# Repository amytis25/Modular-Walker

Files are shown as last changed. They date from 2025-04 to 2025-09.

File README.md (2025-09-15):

ENSC 386 – An Introduction to Mechanical Design and Analysis of Robots

Modular Walker

Due Date: April 27th/ 2025

Amytis Saghafi
asa414@sfu.ca

Simon Schaufele
ses16@sfu.ca

Justin Krohman
jek14@sfu.ca 

Abstract

This project presents the design and analysis of a Modular Walker robot developed to support aging-in-place living. This transformer robot features a modular, self-configurable system that transforms into different modes—walking support, table, and seating—to assist elderly individuals in everyday tasks. Equipped with linear actuators, a call system, and docking capabilities, the design promotes safety, autonomy, and usability. The report outlines the design concept, mechanical analysis, actuation system, and integration within a home environment.
Introduction
The rising elderly population poses challenges for independent living. Robotic systems offer innovative solutions to enhance autonomy and reduce social isolation. This project proposes a transformer robotic system—the Modular Walker—targeted at elderly users who require assistance with mobility, eating, and transitioning between sitting and standing.
Existing Products:
Standard walkers lack dynamic support or smart features.
Sit-to-stand lift chairs offer seating assistance but lack mobility.
Robotic assistants like ElliQ and mobile tables are single-purpose.
Our design combines and extends these functionalities through a reconfigurable robotic system.

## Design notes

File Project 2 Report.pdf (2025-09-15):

ENSC 386 – An Introduction to Mechanical Design and Analysis of Robots

Project 1

# Modular Walker

Due Date: April 27th/ 2025

Contributions

Amytis Saghafi | 301455814 | asa414@sfu.ca | 33%
Simon Schaufele 301454255 | ses16@sfu.ca | 33%
Justin Krohman | 301451597 | jek14@sfu.ca | 33%

## Abstract

This project presents the design and analysis of a Modular Walker robot developed to support aging-in-place living. This transformer robot features a modular, self-configurable system that transforms into different modes—walking support, table, and seating—to assist elderly individuals in everyday tasks. Equipped with linear actuators, a call system, and docking capabilities, the design promotes safety, autonomy, and usability. The report outlines the design concept, mechanical analysis, actuation system, and integration within a home environment.

## Introduction

The rising elderly population poses challenges for independent living. Robotic systems offer innovative solutions to enhance autonomy and reduce social isolation. This project proposes a transformer robotic system—the Modular Walker—targeted at elderly users who require assistance with mobility, eating, and transitioning between sitting and standing.

Existing Products:

- Standard walkers lack dynamic support or smart features.
- Sit-to-stand lift chairs offer seating assistance but lack mobility.
- Robotic assistants like ElliQ and mobile tables are single-purpose.

Our design combines and extends these functionalities through a reconfigurable robotic system.

## Design Problems and Constraints

Design Problem:
To design a multi-purpose robotic walker system that autonomously adapts to support sitting, standing, walking, and meal delivery.

Constraints:

- Must support up to 250 lbs for sitting support.
- Must integrate into typical home layouts.
- Must allow modular reconfiguration and remote control.
- Must use commercially available actuators and parts.

Use Case Layouts & Challenges:

- Bedroom → Living Room
- Supports the user when moving off the bed into a standing position.
- Supports the user when standing as a walker.
- Motorized wheels to alleviate the force required to move the module.
- Supports the user when sitting with back support and a motor lockout to prevent movement.
- Kitchen Docking
- Self-driving to the kitchen station using motors and infrared sensors.
- Automatic alignment with the kitchen module to dock.
- Automatic food delivery onto the walker in table mode.
- Automatic delivery of food to the user using self-driving.
- Challenges
- Navigating cluttered environments with limited sensors.
- Automatic docking and connecting to the bed and kitchen modules.

Design Summary:

- Modular walker with transformable seat/chair
- Bed/chair interface module and kitchen docking.
- Remote summon functionality and self-alignment via sensors.

## Type Synthesis

Considered Concepts:

- Single-purpose walker (too limited)
- Robotic exoskeleton (complex, not modular)
- Multi-purpose transformer walker ✅

After discussing possible ideas for the modular robotic system, it was agreed that the best idea was a multi-purpose walker to support users in a home with the following features:
- Capable of supporting the user as a walker
- Capable of supporting the user as a chair
- Can navigate the living area autonomously
- Walker can switch between walker and chair mode
- Capable of supporting the user in other daily tasks

Walker Module:
- Rigid walker with wheels and sensors to navigate the living area
- Supports the user in navigating the house
- Carrying space to increase the functionality
- Simple design, low functionality, little to no innovation
- Linear actuator walker to switch between a chair & walking mode
- Chair mode allows the user to sit
- Table mode to deliver food
- Moderate complexity, offers innovative support, and is expensive
- Two sets of linear actuators to allow for a floor, chair, & walking
- Chair mode allows the user to sit
- Table mode to deliver food
- More complex design, heavier, & most expensive

Final Concept:
A parallel-bar style modular walker with:
- One set of extendable double-acting cylinders.
- Swappable bed and chair interface modules.
- Docking and delivery module for the kitchen.

## Size Synthesis

### Walker Module

Mode Primary Cylinder Seat/Table Height

Seat | Retracted | 0.58m
Table | Extended | 1m
- Cylinder Stroke: 0.305m
- Total Lift Support: 115kg (safety ratio considered, max support: 185kg)
- Seat Dimensions: 0.4572m x 0.305m
- Dimensions: 0.610m x 0.305m x 0.914m
- Materials: Aluminum frame and supports, canvas seat/table, rubber caster wheels

### Kitchen Module

- Overall Dimensions:
Length: 0.92 m | Width: 0.46 m | Height: 0.20 m
- Base Dimensions:
Length: 0.92 m | Width: 0.43 m | Height: 0.14 m
- Overhang Dimensions:
Length: 0.11 m | Width: 0.46 m | Height: 0.05 m
- Main Belt Length: 1.5641 m
- Secondary Belt Length: 0.2494 m
- Belts Width: 0.32671 m
- Attachment Module: 0.3048 m x 0.2032 m
- Module Mass: 17.5 kg
- Weight Allowance: 7 kg rated, 25 kg max
- Materials: ⅓ infill PC-ABS ( blend of Polycarbonate (PC) and Acrylonitrile Butadiene Styrene (ABS)) Frame, ¼ infill Aluminum Alloy rollers and motor enclosure, rubber belts

### Bed Module

- Contracted Position Dimensions
Length: 0.13m | Width: 0.38 m | Height: 0.44m
- Extended Position Dimensions
Length: 0.13m | Width: 0.38 m | Height: 0.59m
- Bed Frame Hanger: 0.381 m x 0.127 m x 0.0508 m
- Electrical Actuators: 0.279 m x 0.432 m x 0.0381 m
- Wheel Bed: 0.114 m x 0.0381 m x 0.029 m
- Module Mass: 4.83 kg
- Actuator Stroke Length: 0. 152 m
- Materials: Aluminum frame supports supports Aluminum Actuators and Polyethylene Wheelbed

## Detailed Component Design

### Modules & Features:

- Main Frame: Parallel bar design with height-changing table.
- Cylinders:
- Primary: 102 lbs force @ 100 psi
- Support Beam: Reinforced crossbeam at the top and bottom of the cylinders.
- Piston Mounts: Mounts directly to the base and crossbeams
- Remote & Sensor Unit: Bluetooth or Wi-Fi controlled; IR or ultrasonic for alignment.

### Module 1 - Walker Module

Configurations:
- Walker mode - Seat at 0.585m, Wheels moving
- Chair mode - Seat at 0.585m, Wheels locked out
- Table mode - Seat at 1m, Wheels moving, Locked out wheels at Kitchen and Bed module

Size:

Length: 0.56 m | Width: 0.33 m | Height: 1.02 m

Materials:

- Aluminium components

Movement:

The module moves using two motors for the front two wheels. The wheels rotate as the walker is pushed in walker mode. Infrared sensors guide the module to the required location, allowing it to move autonomously. The module can self-drive between the kitchen, bed, and the user. The user can control the module with a remote, which can change the configuration or send it to a location.

### Module 2 - Kitchen Module

Configuration:

- The base portion of the module lies on top of the kitchen counter with the overhang portion resting against the side of the counter.
- The overhang portion includes a proximity sensor and electromagnets. The proximity sensor activates the electromagnets to hold the walker in place as the module moves an object (e.g., a plate of food) onto the walker.

Size:

- Overall:
Length (x): 0.92 m | Width (y): 0.46 m | Height (z): 0.20 m
- Base:
Length (x): 0.92 m | Width (y): 0.43 m | Height (z): 0.14 m
- Overhang:
Length (x): 0.11 m | Width (y): 0.46 m | Height (z): 0.05 m
Materials:
- PC-ABS ( blend of Polycarbonate (PC) and Acrylonitrile Butadiene Styrene (ABS))
- Aluminium Alloy
- Rubber

Movement:

This module uses a compact DC motor to rotate the first set of rollers attached to the motor using bevel gears. The main belt of this module rotates around the rollers, carrying an object (a plate filled with food) to the next belt, which will move with the force of the object's already existing acceleration as well as the force of gravity, as the secondary belt has approximately a 20-degree decline. Following the second belt, the object will be smoothly pushed onto the “table” portion of the walker.

Attachment:

Attaches to the kitchen module using electromagnets, and a sensor detects the walker's presence.

### Module 3 - Bed Module

Configuration:
- Compacted: The actuators are retracted to reduce the footprint of the module
- Extended: The IR Sensors have detected that the module has been deployed and signal the Arduino to self configure
Size
Length: 0.13m | Width: 0.38 m | Height: 0.59m

Materials: Aluminum alloy and Polyethylene
Movement: Two Electrical actuators receive a signal from IR sensors in the modules hanging attachment. This signals them that the module has been deployed. The actuators then lengthen to fit the size of the bed frame that the module is attached to.
Attachment: The Walker Attaches to the bed module using electromagnets and a sensor to detect the walkers presence

## Specifications

Actuators:
Walker Module
- McMaster Impact-Resistant Round Body Air Cylinders (https://www.mcmaster.com/6471K334/)
- Air-driven, 102 lbs @ 100 psi each
- Mounted with guiding rails and locking mechanisms
- Air compressor (https://www.amazon.ca/HOTTQUE-Multifunctional-Inflator-Compressor-Motorcycle/dp/B0DFM3JPHX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)
- Motors (https://ca.robotshop.com/products/e-s-motor-12v-16rpm-high-torque-dual-shaft-31d-motor-w-worm-gear-reduction-with-customized-connector-terminations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)
- Front Wheels, (https://ca.robotshop.com/products/sparkfun-wheel-65mm-rubber-tire-pair?qd=a9e12b3ea89f7583d59347062a0848af) Back (https://www.rona.ca/en/product/madico-general-duty-rubber-plate-caster-brake-44-lbs-1-1-2-f22904-01015307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) Wheels
Kitchen Module
- Compact Round-Face DC Motor (https://www.mcmaster.com/6331K65/)
- Motor Speed: 4535 rpm @ 0.0812 N-m
- Starting Torque: 0.5437 N-m
- Required torque: 4.14 N-m
■ τ
required = F
friction
| × radius = 9. 81M
Max
| | × µ = 108. 69 × 0. 5 = 4. 14
■ Note: This calculation is for an unlubricated system; a lubricated system would need significantly less torque.
- Roller Gear to Motor Gear ratio: 8:1
- 5V Electromagnet (https://www.digikey.ca/en/products/detail/adafruit-industries-llc/3874/9603613)

Bed Module

- McMaster Electric Actuator (https://www.mcmaster.com/6509K56/)
- 11.3kg Dynamic load capacity
- 136kg static load capacity
- Maximum speed 76.2mm/s
- 5V Electromagnet
Motion Transmission:
- Linear lifting via cylinder extension (Walker Module)
- Load transfer through piston brackets and reinforced beams (Walker Module)
- Rotational motion transmission via bevel gears (Kitchen Module)

Control Source:
- IR Sensors (https://www.amazon.ca/C-J-Infrared-Obstacle-Avoidance-Arduino/dp/B00XAGSWR4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)
- Arduino Uno (https://www.amazon.ca/Elegoo-Board-ATmega328P-ATMEGA16U2-Arduino/dp/B01EWOE0UU?hvadid=208414040833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)
- ROS-based command structure

## Case Study Static Analysis

### Walker Module

Payload:
- Max load: 250 lbs = 1113 N
- Cylinder support force: 400 lbs = 1780 N
- Safety ratio: 1.6
Weight:
- Walker module total mass: 21kg = 206.01 N
- Seat mass: 2kg = 19.62 N
- Cylinder mass: 1.5kg = 14.715 N (each)
- Base mass: 7.5kg = 73.575 N
- Supports mass: 6kg = 58.86 N
Tipping Analysis:
- Consider CoG shift during transformation
- Counterbalanced base and locking wheels prevent forward tipping
- Simulation to confirm balance under 40” extended table height with load

Static stability analysis:
Centre of mass location: X - .200m Y - .380m Z - .125m (related to the bottom wheel)
Angle of tipping: Θ = arctan( | (tipping can only occur around the z-axis as the .200
.380

) = 27. 76°
module would roll in any other direction)
Max Horizontal Force: Θ＜arctan(

Max Force
Total Mass

)
Max Force = 206 tan(27. 76°) = 108. 5N

### Kitchen Module

Payload:
- Max load: 25 kg
Weight:
- Kitchen module total mass: 17.5 kg = 171.675 N
- Frame mass: 6.23 kg = 61.1163 N
- Rollers mass: 9.56 kg = 93.7836 N
- Main belt mass: 1.08 kg = 10.5948 N
- Secondary belt mass: 0.09 kg = 0.8829 N
- Motor and enclosure mass: 0.27 kg = 2.6487 N Attached Actuators:
- 2x electromagnets

Static Stability Analysis:
Center of mass relative to the back bottom corner of the base: X = 0.47 m, Y = 0.2 m, Z = 0.06 m For the structure to tip over, the center of gravity's X component must be located past 0.75 m. To see how much weight would shift the center of gravity past the tipping point, the following calculations were done:

X

tip =

mstructure

x

structure +mobjectx
object
mstructure+mobject

→ 0. 75 =

(17.5)(0.47)+(0.92)mobject

17.5+mobject

Solving for mobject

, it is determined that the object must weigh 28.8 kg or more to cause the module to tip over and fall off the counter when the object reaches the end of the belt. Since the module has a maximum load capacity of 10 kg, tipping over is not a concern.

To make sure the object won’t slip off the secondary belt, the maximum acceleration of the object can be calculated as shown below (note: the coefficient of static friction between dry glass and rubber was used):

ΣF = ma → F

friction = ma → 9. 81sin(20)m = ma → a = 0. 73 m/s

2

As shown above, the maximum acceleration allowed is 0.73 m/s² to prevent the object from slipping on the belt's surface.

### Bed Module

Payload:
- Max Load: 300 lbs = 1335 N Weight:
- Arduino uno: 11.83 g = 0.1160523 N
- Hanging frame: 2.98 kg = 29.2338 N
- Electromagnets: 22.2 g = 0.217782 N
- Electric actuators: 1.72 kg = 16.8732 N
- Wheelbeds = 94.5 g = 0.927045 N Attached Actuators:
- 2x electromagnets
- 2x Linear Actuators

Static Stability Analysis:
The center of mass relative to the back corner of the left wheel bed:
X = 18.67cm, Y = 42.79cm, Z = 0.88cm
The bed module is suspended from the bed frame, and the wheel beds rest on the ground. This means that, to tip the bed module, it would either need to be disconnected from the bed frame or the bed frame itself would have to tip over. Therefore, the tipping point is determined by the stability of the bed frame. The module itself is not designed to support any weight other than the walker wheels in the wheel beds, which are in contact with the ground. Since this weight is also supported by the ground, the maximum load on the module would be the combined weight of the walker module and the person.
The pressure exerted by one of the wheels when the person leans on it is approximately one quarter of the combined weight of the person and the walker (75lb). Given that the compressive strength of polyethylene is about 3000 psi (20.7MPa), the wheel beds can support the maximum payload without any deformation. This is shown below (note: wheel bed area = 1.69 in²
):
σ =

F
A

→ σ =

2413
1.69 = 1427 psi
This is much less than the allowable compression strength of the wheel bed.

## Image and Animated Videos

Note: Videos of the modules can be viewed in the project folder under images directory/ animation, as they cannot be added to this document.

### Walker Design

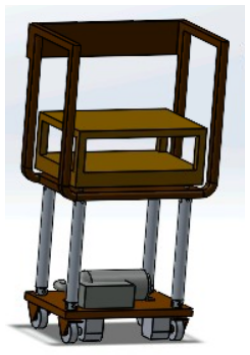
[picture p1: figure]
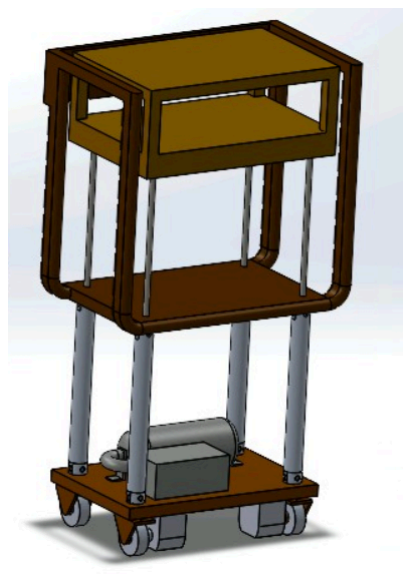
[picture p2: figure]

Chair & Walker Configuration | Table Configuration

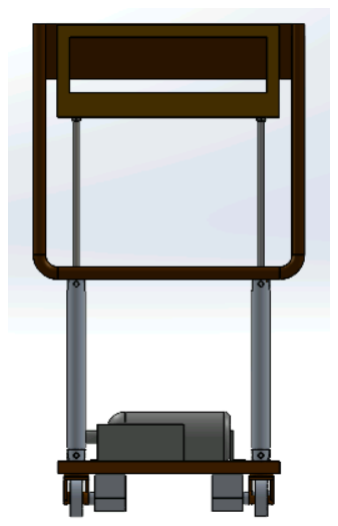
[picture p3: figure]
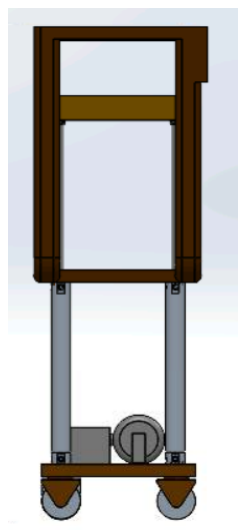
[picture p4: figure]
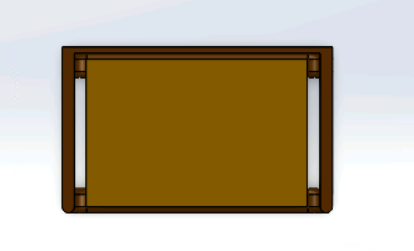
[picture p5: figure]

Front View | Side View | Top View

### Kitchen Module

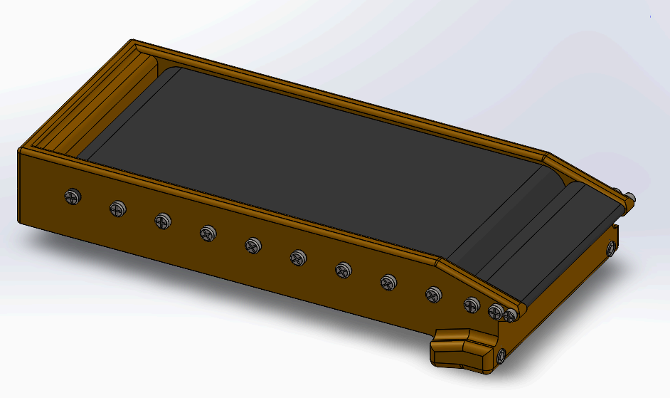
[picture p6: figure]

Kitchen Module Simulation

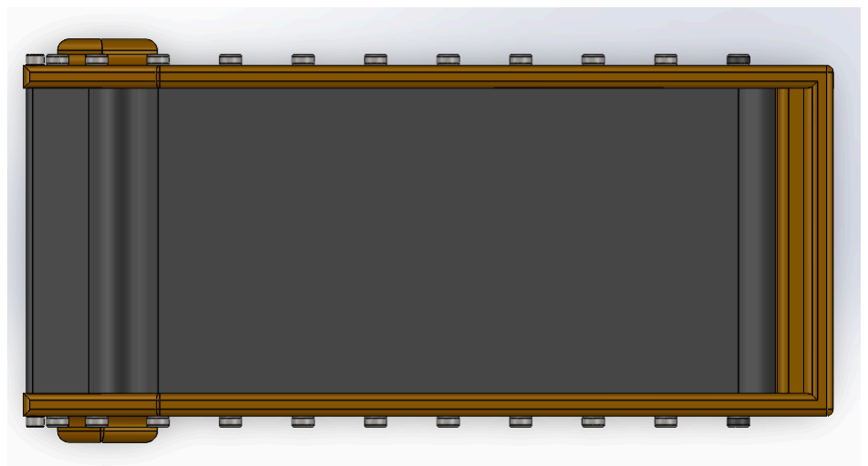
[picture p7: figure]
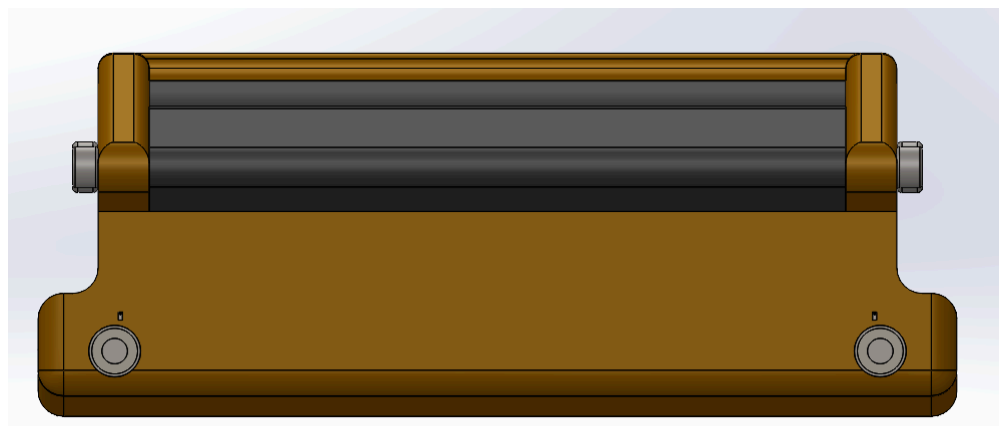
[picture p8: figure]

Top View of the Kitchen Module | Front View of the Kitchen Module

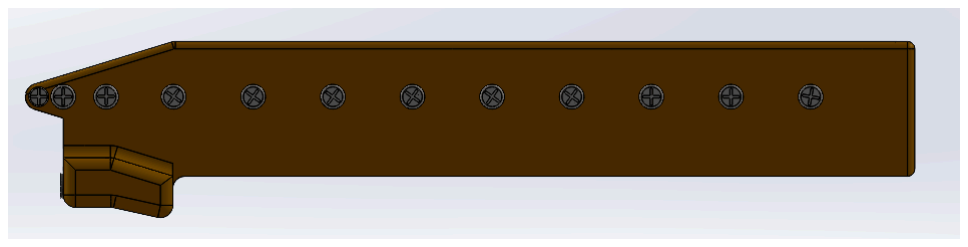
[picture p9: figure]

Side View of the Kitchen Module

The hidden lines visible model shown below shows More Detail, including pathways for wiring and cavities for circuitry, batteries, fans, etc.

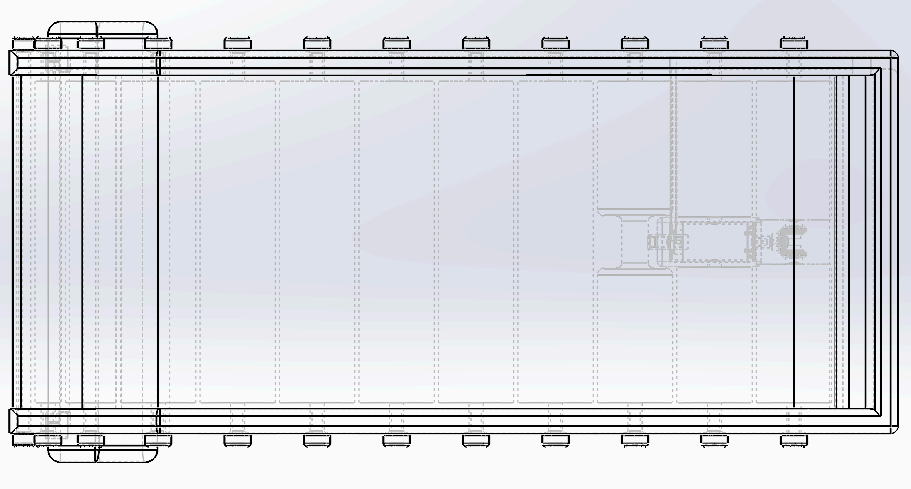
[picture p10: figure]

Top View of the Kitchen
Module

Side View of the Kitchen
Module

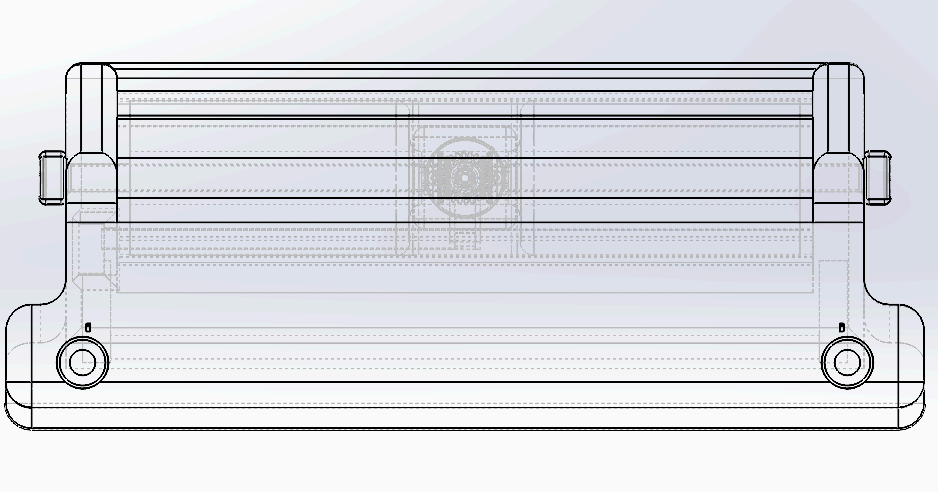
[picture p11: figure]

Front View of the Kitchen
Module

### Bed Module

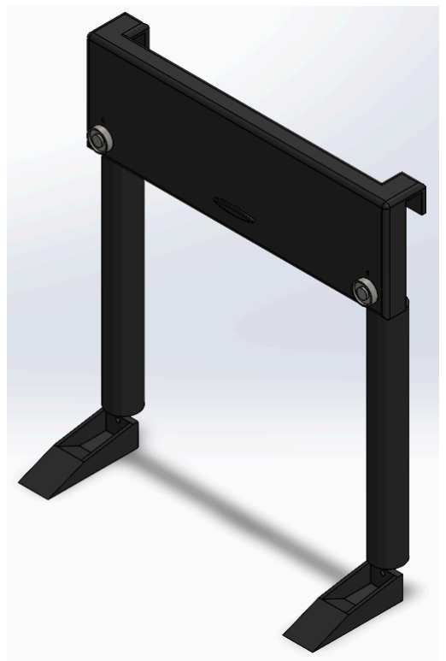
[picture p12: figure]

Bed Module Simulation

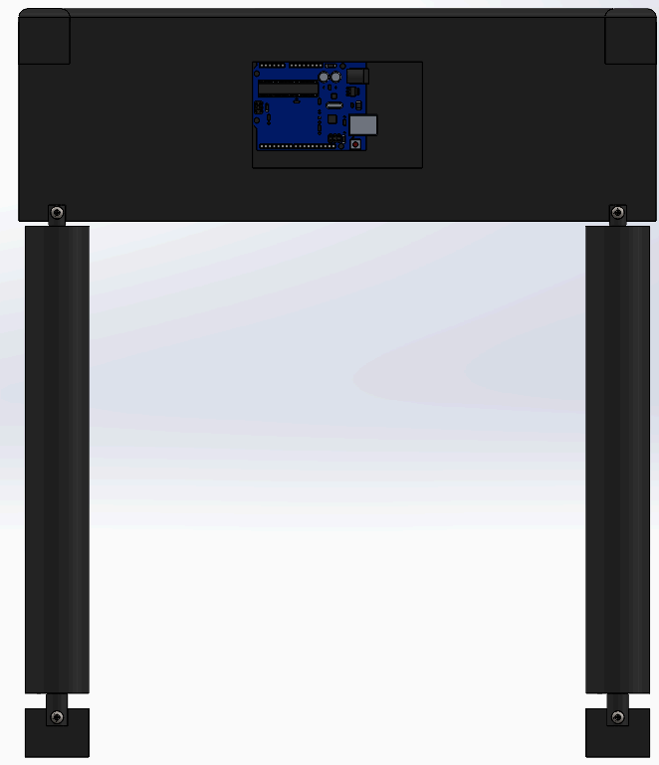
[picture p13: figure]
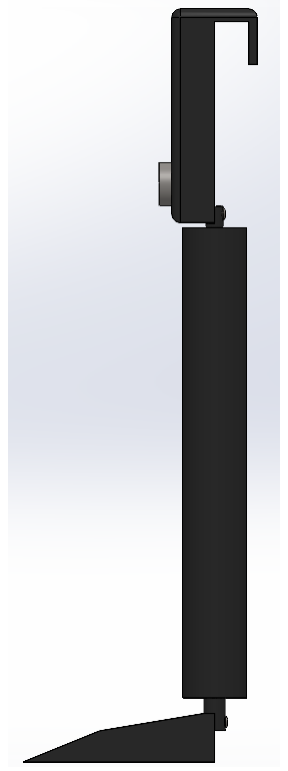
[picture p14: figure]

Side View of the Bed Module | Front View of the Bed Module

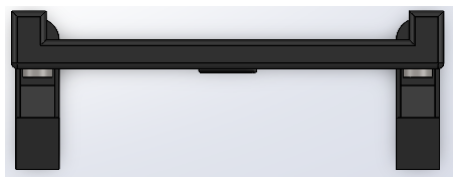
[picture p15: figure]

Top View of the Bed Module

## Discussion and Future Work

The Modular Walker fulfills key functions for elderly care in a modular form. The design fulfills all the functionalities specified in the synthesis design, which supports the user moving around their home and performing daily tasks like food delivery. These functions are fulfilled using three modules: the walker module, the bed module, and the kitchen module.

The walker module is the primary component that the user interacts with. This module supports the user when moving around their home and provides a place to sit anywhere. The walker can be summoned or its configuration changed using a Wi-Fi button remote.

The bed module connects to the walker and provides a place for the walker to be stored and charged when not in use. It can also help the user get out of bed and into a standing or seated position on the walker.

The kitchen module connects to the walker through electromagnets. This connection ensures the walker's position is accurate and provides a direct connection to ensure the walker is in the correct configuration. This module delivers food onto the walker, placing a plate onto the walker in table mode. The walker then disconnects from the kitchen module and autonomously delivers the food to the user.

Future improvements include:

- A more stable design which is not prone to tipping
- Battery-powered air compressor for cylinder actuation
- Enhanced sensor fusion for better alignment
- Voice control or integration with smart home systems
- Enhanced wheel design to navigate around tight spaces and corners
- An adjustable seat height to maximize the comfort of the user
- More sensors, such as load cells, to allow more accuracy while completing tasks
- i.e. load cell kitchen module to ensure full transfer of object.

## References

[1]
“12V 16rpm High Torque Dual Shaft 31D Motor w/ Worm Gear Reduction, with customized connector terminations,” RobotShop Canada. Accessed: Apr. 26, 2025.
[Online]. | | Available:
https://ca.robotshop.com/products/e-s-motor-12v-16rpm-high-torque-dual-shaft-31d-moto r-w-worm-gear-reduction-with-customized-connector-terminations (https://ca.robotshop.com/products/e-s-motor-12v-16rpm-high-torque-dual-shaft-31d-motor-w-worm-gear-reduction-with-customized-connector-terminations)
| | [2]
“3874 Adafruit Industries LLC | Maker/DIY, Educational | DigiKey.” Accessed: Apr. 26,
2025. | [Online]. | Available:
https://www.digikey.ca/en/products/detail/adafruit-industries-llc/3874/9603613
| | [3]
“DAOKI 5-Pack IR Infrared Obstacle Avoidance Sensor Module for Arduino Smart Car Robot 3 Wire : Amazon.ca: Tools & Home Improvement.” Accessed: Apr. 26, 2025.
[Online]. | | Available:
https://www.amazon.ca/C-J-Infrared-Obstacle-Avoidance-Arduino/dp/B00XAGSWR4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 (https://www.amazon.ca/C-J-Infrared-Obstacle-Avoidance-Arduino/dp/B00XAGSWR4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)
| | [4]
“ELEGOO UNO R3 Board ATmega328P with USB Cable(Arduino-Compatible) for Arduino : Amazon.ca: Electronics.” Accessed: Apr. 26, 2025. [Online]. Available: https://www.amazon.ca/Elegoo-Board-ATmega328P-ATMEGA16U2-Arduino/dp/B01EWOE0UU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 wFPTQYc-R2bbAitwRYlXgVksVoz7wd1v5umHaJ4wKbGjXJ9GZJfEifSVXSnIDzPoZx FHzU.V25m7TA22pPwS6tTp7w2oaZO8PYytDoRU5MG3Xz9_y8&dib_tag=se&hvadid= 208414040833&hvdev=c&hvlocphy=9001527&hvnetw=g&hvqmt=e&hvrand=24032207 0627911368&hvtargid=kwd-295449705573&hydadcr=20846_9881421&keywords=ardui no&mcid=f5570030f4b73130814adeb55dc1fd80&qid=1744753651&sr=8-2-spons&sp_cs d=d2lkZ2V0TmFtZT1zcF9hdGY&psc=1 (https://www.amazon.ca/Elegoo-Board-ATmega328P-ATMEGA16U2-Arduino/dp/B01EWOE0UU?hvadid=208414040833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)

[5]
“HOTTQUE Multifunctional Tire Inflator Portable Air Compressor Cordless Tire Inflato 150 PSI with Digital Pressure Gauge 12V Smart Air Pump for Car Tires, Motorcycle, SUV, Bicycle, Sports Balls…, Air Compressors - Amazon Canada.” Accessed: Apr. 26,
2025. | | [Online]. | | | | Available:
https://www.amazon.ca/HOTTQUE-Multifunctional-Inflator-Compressor-Motorcycle/dp/B0DFM3JPHX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 (https://www.amazon.ca/HOTTQUE-Multifunctional-Inflator-Compressor-Motorcycle/dp/B0DFM3JPHX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)
| | | | | | [6]
“MADICO General-Duty Rubber Plate Caster - Brake - 44 lbs - 1 1/2" F22904 | RONA.”
Accessed: | Apr. | 26, | 2025. | [Online]. | Available:
https://www.rona.ca/en/product/madico-general-duty-rubber-plate-caster-brake-44-lbs-1-1-2-f22904-01015307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 QjwiLLABhCEARIsAJYS6ukSUs28AxclCiFWawiKpM8Q-xoJayHchAjmwjO3-tk8eWZ v9tO-bqYaAgNpEALw_wcB&gclsrc=aw.ds (https://www.rona.ca/en/product/madico-general-duty-rubber-plate-caster-brake-44-lbs-1-1-2-f22904-01015307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)
| | | | | | [7]
“McMaster-Carr.” | Accessed: | Apr. | 26, | 2025. | [Online]. | Available:
https://www.mcmaster.com/6509K56/
| | | | | | [8]
“McMaster-Carr.” | Accessed: | Apr. | 26, | 2025. | [Online]. | Available:
https://www.mcmaster.com/6331K65/
| | | | | | [9]
“McMaster-Carr.” | Accessed: | Apr. | 26, | 2025. | [Online]. | Available:
https://www.mcmaster.com/6471K334/
| | | | | | [10]
“Sparkfun Wheel - 65Mm (Rubber Tire, Pair),” RobotShop Canada. Accessed: Apr. 26,
2025. | | [Online]. | | | | Available:
https://ca.robotshop.com/products/sparkfun-wheel-65mm-rubber-tire-pair

## Appendices

### Appendix A - SolidWorks Files

A.1 Walker Module

Air_Compressor.SLDPRT - Air compressor to refill the air storage Air_Storage.SLDPRT - Air storage compartment Base_6471k334_Impact-Resistant Round Body Air Cylinder.SLDPRT - Base of the cylinders
Rod_Cylinder.SLDPRT - The extending cylinder rod
Cylinder_Top_Plate.SLDPRT - The top plate and arm supports
Motor.SLDPRT - Motors for the front wheels Seat_Table2.SLDPRT - The Seat and Table the changes height Wheel.SLDPRT - Wheels for the base
Assem2.SLDASM - Fully Assembled design of the walker

A.2 Kitchen Module
0.5in-roller.SLDPRT - 0.5 inch roller 1in-roller.SLDPRT - 1 inch roller
2in-roller.SLDPRT - 2 inch roller
3in-roller.SLDPRT - 3 inch roller
3in-roller-gear-attachment.SLDPRT - 3 inch roller which attaches to a Metal bevel Gear
3in-roller-motor-attachment.SLDPRT - 3 inch roller which attaches to a the side of the motor enclosure
3in-roller-motor-cutout.SLDPRT - 3 inch roller with the middle thinned out to allow for the motor enclosure
6331K65_Compact Round-Face DC Motor.SLDPRT - Model of the DC motor (from Manufacturer)
6529K53_Metal Miter Gear.SLDPRT - Model of a bevel gear motorbox.SLDPRT - Enclosure for the motor housing.SLDPRT - Frame and base for the entire module motor-gear-connector.SLDPRT - A piece for motor and bevel gear connection electromagnet.SLDPRT - Rough model of the 5V Electromagnet sensor.SLDPRT - Rough model of the proximity sensor
plate.SLDPRT - Rough model of a plate for simulation purposes boxed-motor.SLDASM - Assembly of the enclosed motor final-assembly.SLDASM - Complete assembly of the kitchen module

A.3 Bed module

hanger.SLDPRT - Hangs the module to the frame of the user’s bed Arduino_Uno.STEP - Model of Arduino Uno (from Manufacturer)
screw.SLDPRT - Screw used for assembling the module
piston rod.SLDPRT - Extending rod of the electric actuator
wheelbed.SLDPRT - Holds the wheels of the walker stable when it is docked at the bed module
piston body.SLDPRT - Aluminum body of the electric actuator
electromagent.SLDPRT - Rough model of the 5V Electromagnet Arduino_Uno.SLDPRT - Model of Arduino Uno (from Manufacturer) Assem1.SLDASM - Final Assembly of the bed module

### Appendix B – Technical specification of the selected actuators and sensors

B.1 Actuators

B.1.1 Walker Module
Actuator 1: McMaster Impact-Resistant Round Body Air Cylinders
- Part Number: 6471K334
- Type: Double-acting pneumatic cylinder
- Force: 102 lbs (454 N) @ 100 psi
- Stroke: 0.305 m (12 inches)
- Mounting: Guided rails with locking mechanism
- Safety Ratio: 1.6 (max support: 185 kg / 408 lbs)
- Application: Seat/table height adjustment (0.58m retracted → 1m extended).
- Vendor: McMaster-Carr
Actuator 2: Air Compressor
- Type: Portable electric air compressor (to power cylinders)
- Pressure: 100 psi minimum
- Duty Cycle: Continuous (for repeated actuation)
- Future Upgrade: Battery-powered compressor (e.g., VIAIR 90P).

B.1.2 Kitchen Module
Actuator 1: Compact Round-Face DC Motor
- Part Number: 6331K65
- Speed: 4535 RPM @ 0.0812 N-m
- Starting Torque: 0.5437 N-m
- Gear Ratio: 8:1 (motor-to-roller)
- Output Torque: 4.14 N-m (after gearing)
- Application: Drives kitchen module’s main belt for food transfer.
- Vendor: McMaster-Carr
Actuator 2: 5V Electromagnets
- Holding Force: 10 kg (per magnet)
- Voltage: 5V DC
- Quantity: 2 (for docking alignment)
- Application: Secures walker module to kitchen station during food transfer.
- Vendor: Digikey

B.1.3 Bed Module
Actuator 1: Electric Linear Actuator
- Type: Battery-powered linear actuator (to replace pneumatic cylinders)
- Stroke: 0.152 m
- Load Capacity: 300 lbs (136 kg)
- Speed: 76 mm/s (adjustable)
- Application: Delopy the wheel beds

Actuator 2: 5V Electromagnets
- Holding Force: 10 kg (per magnet)
- Voltage: 5V DC
- Quantity: 2 (for docking alignment)
- Application: Secures walker module to kitchen station during food transfer.
- Vendor: Digikey
B.2 Sensors

B.2.1 Walker Module
Sensor 1: Infrared (IR) Proximity Sensors
- Type: IR reflectance sensor
- Detection Range: 0.1–0.8 m
- Interface: Digital I/O
- Application: Autonomous navigation and alignment with bed/kitchen modules. Sensor 2: Wheel Encoders
- Type: Optical rotary encoder (integrated with motors)
- Resolution: 12 pulses per revolution (PPR)
- Application: Speed/distance tracking for motorized wheels.

B.2.2 Kitchen Module
Sensor 1: Proximity Sensor With Interrupt, IRED, and I2C Interface
- Part Number: 751-VCNL3040TR-ND - Tape & Reel (TR)
- Detection Range: 0–300 mm
- Interface: I2C
- Application: Detects walker module for docking alignment.
- Vendor: DigiKey/RobotShop

B.2.3 Bed Module
Sensor 1: Proximity Sensor With Interrupt, IRED, and I2C Interface
- Part Number: 751-VCNL3040TR-ND - Tape & Reel (TR)
- Detection Range: 0–300 mm
- Interface: I2C
- Application: Detects walker module for docking alignment.
- Vendor: DigiKey/RobotShop
B.3 Controllers

Controller 1: Raspberry Pi 4
- Processor: Broadcom BCM2711 (Quad-core Cortex-A72)
- RAM: 4GB
- Connectivity: WiFi/Bluetooth
- Role: ROS-based navigation, sensor fusion, and user command processing.

Controller 2: Arduino Uno
- Microcontroller: ATmega328P
- Clock Speed: 16 MHz
- Analog Inputs: 6
- Role: Real-time motor control, sensor polling, and electromagnet activation.

### Appendix C - Suggestions for supporting hardware and electronics

C.1 Controllers

1. Raspberry Pi 4
- Part Number: N/A (Standard model)
- Description: Quad-core Cortex-A72 processor, 4GB RAM, Wi-Fi/Bluetooth.
- Purpose: ROS-based navigation, sensor fusion, and user command processing.
- Supplier: Electronics retailers (e.g., Amazon, Adafruit).
2. Arduino Uno
- Part Number: ELEGOO UNO R3 [4]
- Description: ATmega328P microcontroller, 16 MHz clock speed.
- Purpose: Real-time motor control, sensor polling, and electromagnet activation.
- Supplier: Amazon.
C.2 Sensors
1. Infrared (IR) Proximity Sensors
- Part Number: DAOKI 5-Pack IR Sensor [3]
- Description: 3-wire IR reflectance sensor, 0.1–0.8 m range.
- Purpose: Autonomous navigation and docking alignment.
- Supplier: Amazon.
2. Proximity Sensor (I2C Interface)
- Part Number: 751-VCNL3040TR-ND [2]
- Description: IRED sensor with 0–300 mm detection range.
- Purpose: Precise alignment for kitchen and bed module docking.
- Supplier: DigiKey.
3. Wheel Encoders
- Part Number: Integrated with motors (e.g., Sparkfun wheels [10]).
- Description: Optical rotary encoder, 12 PPR resolution.
- Purpose: Speed/distance tracking for motorized wheels.

C.3 Actuators
1. Double-Acting Pneumatic Cylinders
- Part Number: McMaster 6471K334 [7]
- Description: 102 lbs force @ 100 psi, 0.305 m stroke.
- Purpose: Walker seat/table height adjustment.
- Supplier: McMaster-Carr.
2. Electric Linear Actuators
- Part Number: McMaster 6509K56 [8]
- Description: 136 kg static load capacity, 76.2 mm/s speed.
- Purpose: Bed module deployment.
- Supplier: McMaster-Carr.
C.4 Motors
1. Compact DC Motor (Kitchen Module)
- Part Number: McMaster 6331K65 [8]
- Description: 4535 RPM, 0.5437 N-m starting torque.
- Purpose: Drives kitchen conveyor belt via 8:1 gear ratio.
- Supplier: McMaster-Carr.
2. Wheel Motors
- Part Number: 12V 16RPM High Torque Motor [1]
- Description: Worm gear reduction, dual shaft.
- Purpose: Front-wheel drive for walker module.
- Supplier: RobotShop.
C.5 Power and Communication
1. Portable Air Compressor
- Part Number: HOTTQUE Cordless Inflator [5]
- Description: 100 PSI, battery-powered.
- Purpose: Pneumatic cylinder actuation.
- Supplier: Amazon.
2. 5V Electromagnets
- Part Number: Adafruit 3874 [2]
- Description: 10 kg holding force.
- Purpose: Secures walker during docking.
- Supplier: DigiKey.
3. Wi-Fi/Bluetooth Module
- Description: ESP32 or similar.
- Purpose: Remote control and ROS integration.

C.6 Safety and Miscellaneous
1. Emergency Stop Button
- Description: Physical kill switch for immediate shutdown.
2. Load Cells
- Purpose: Future upgrade for weight detection (e.g., kitchen module).
3. Rubber Belts and Rollers
- Part Number: Custom (see Appendix A.2).
- Supplier: McMaster-Carr/3D-printed.

### Appendix D - Bill of Materials

D.1 Walker Module

Component | Qty | Part Number | Description | Supplier
Linear Actuators | 2 | 6471K334 [7] | Double-acting pneumatic cylinders | McMaster-Carr
Rubber Caster Wheels | 4 | MADICO F22904 [6] | 1.5" brake wheels, 44 lbs capacity | RONA
IR Proximity Sensors | 4 | DAOKI 5-Pack [3] | Obstacle avoidance | Amazon
Arduino Uno | 1 | ELEGOO UNO R3 [4] | Microcontroller | Amazon
Air Compressor | 1 | HOTTQUE [5] | 100 PSI portable compressor | Amazon
Aluminum Frame | 1 | Custom | 6061-T6 aluminum bars | Local supplier
Canvas Seat | 1 | Custom | 0.4572m x 0.305m seat | Fabric supplier

D.2 Kitchen Module

Component | Qty | Part Number | Description | Supplier
DC Motor | 1 | 6331K65 [8] | Compact round-face motor | McMaster-Carr
Bevel Gears | 3 | 6529K53 [A.2] | Metal miter gears for 8:1 ratio | McMaster-Carr
Proximity Sensor | 2 | 751-VCNL3040T R-ND [2] | I2C IR sensor for docking | DigiKey
Electromagnets | 2 | Adafruit 3874 [2] | 5V holding magnets | DigiKey
PC-ABS Frame | 1 | Custom | 3D-printed frame (⅓ infill) | Local printer
Rubber Belts | 2 | Custom | 0.32671m width | McMaster-Carr

D.3 Bed Module

Component | Qty | Part Number | Description | Supplier
Electric Linear Actuators | 2 | 6509K56 [8] | 136 kg static load capacity | McMaster-Carr
Polyethylene Wheelbeds | 2 | Custom | 3D-printed supports | Local printer
Electromagnets | 2 | Adafruit 3874 [2] | 5V holding magnets | DigiKey
Arduino Uno | 1 | ELEGOO UNO R3 [4] | Microcontroller | Amazon
Aluminum Hangers | 1 | Custom | 0.381m x 0.127m frame | Local supplier
Proximity Sensor | 4 | 751-VCNL3040T R-ND [2] | I2C IR sensor for docking | DigiKey

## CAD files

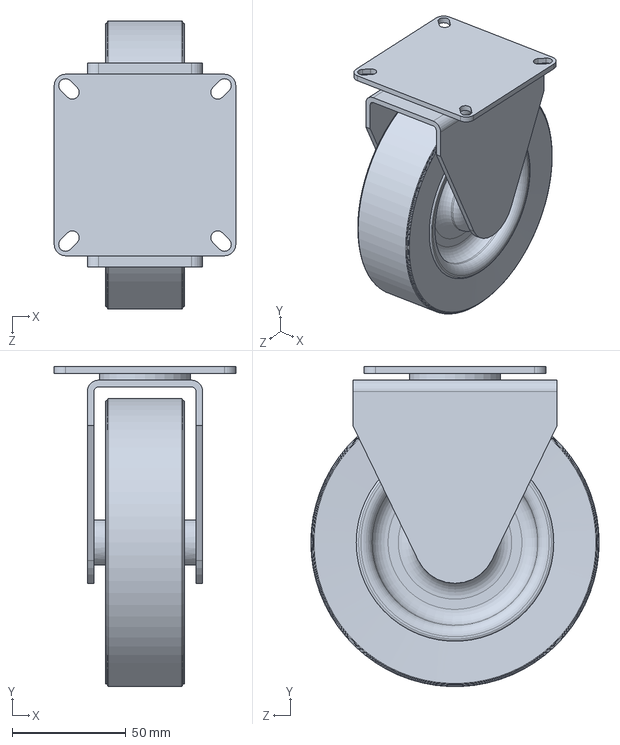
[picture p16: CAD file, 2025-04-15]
1-C-2023-FRONT WHEEL.SLDPRT
80.0 x 140.9 x 127.0 mm

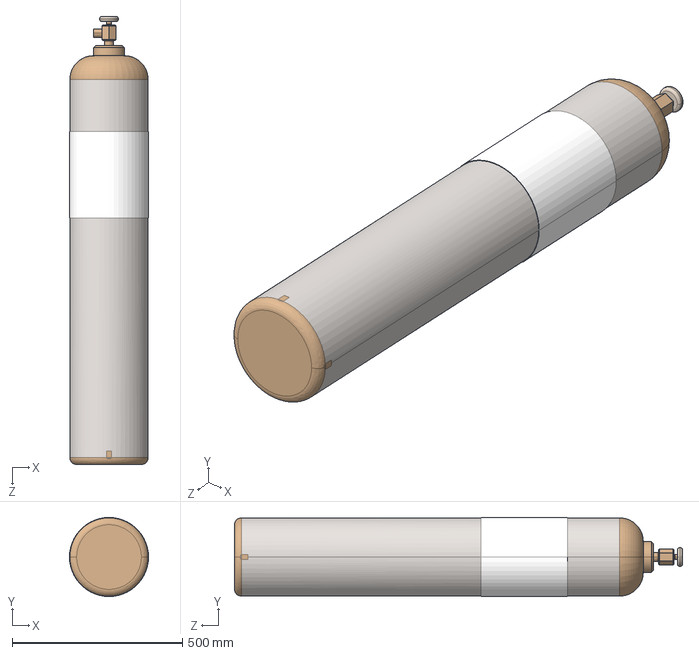
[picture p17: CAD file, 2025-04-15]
cylinder.STEP
232.1 x 232.1 x 1315.0 mm
